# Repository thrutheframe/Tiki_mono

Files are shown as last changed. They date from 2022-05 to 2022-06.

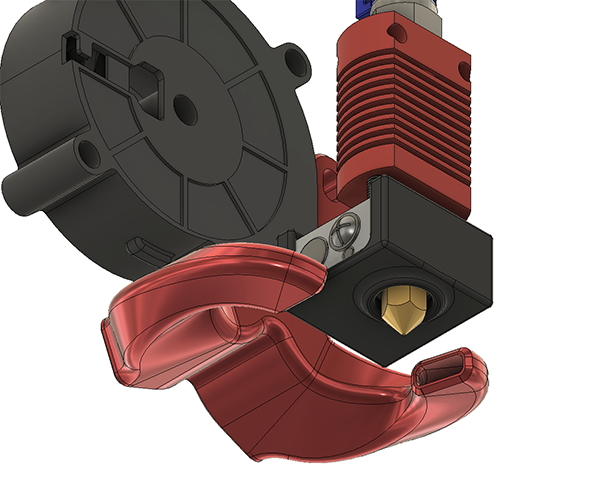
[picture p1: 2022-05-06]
images/5015 fanduct 02.png

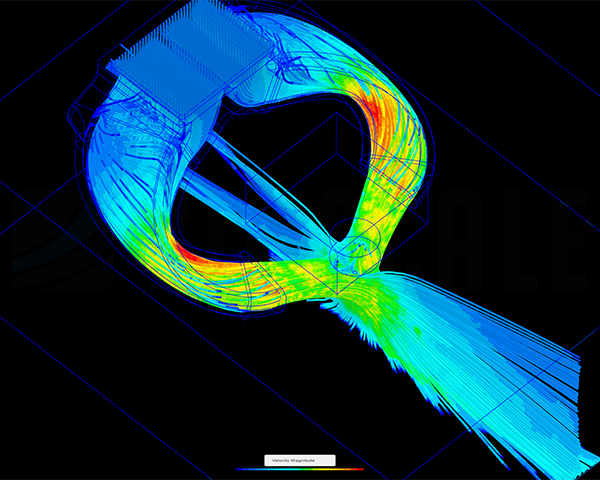
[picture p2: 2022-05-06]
images/CFD 1.png

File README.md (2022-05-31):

# Tiki Monocoque 

Tiki Mono 01

## UPDATE: 31 May 2022
Finding on Tiki Monocoque when I did input shaper calibration using ADXL345 https://github.com/thrutheframe/Tiki_mono/blob/main/update220531.md

## Introduction
Welcome to Tiki Monocoque github page. 

Since the launch of Tiki 3.2 in September 2021, I had done several updates to the design to improve the overall printability and functionality. In addition, I have been working on other projects ie the Donki direct drive extruder and had learned alot (and still learning) in terms of designing a carriage and fan mount system.  In the 2022, I set out to do several things. Learn how use Klipper (done), design and build a bare-bone printer (in progress) and do an update on the Tiki system. 

The original goal of the designing the Tiki was to have a better fanduct system for creality Ender 5. But as time pass, and buying an Orbiter V1.5, I decided to adapt the design for it. That is how Tiki3 came about. Initially my design of the main body takes inspiration from Hangtight (thingiverse) with the side mounted hotend fan and front mounting fanduct. To put things into persepctive, I did not recieve any help nor step files from anyone. I redesign it from ground up to improve printability, incoporated BL touch bracket, cable relief and a mount for the Orbiter. At that time, only thing that I used was the fanduct design because my Fusion360 skills were not good enough. Subsequently, I design the my own 5015 fan duct from scratch. 

Following the path of Tiki3, Tiki Monocoque is designed to support the Orbiter V1.5. If you like using the design and want to support my work, a contribution to my fun-funds at https://www.paypal.com/paypalme/shannonheng will be greatly apperciated. If you want to use the design for commerical/academical intend, do contact me for permission or collaborations. 

## Description
Tiki Monocoque as its namesake is a one piece printed body construction with the fanduct, BL Touch, Orbiter and ADXL345 mounted to it. This approach in design improves rigidity and dimension accuracy. The fanduct is re-wored with input from previous designs. All parts are design with intergrated supports. The fanduct is designed with overhangs of under 60 degree to the horizon. Tiki Monocoque will only work with the parts it is design with. It is lighter that its predecessor, use less material/screws and less parts to print. Please read the instructions below. 

Tiki Monocoque is designed for Creality Ender and CR machines, namely
- Ender 3/3pro/3V2
- Ender 5/5pro/5plus
- CR10 (old version)
- Ender clones with same M5 and screw positions

Hotend that has been designed for:
- Creality stock CR10 hotend (tested)
- Mellow NF-Zone CR10 (tested)
- Mellow NF Zone CR10 (tested)
- Mellow NF-Smart 
- MicroSwiss All Metal and clones

## Instructions
<i>The Instructions section will be updated accordingly when needed.</i>
- You need to reuse the 4010 coaxial fan to cool the hotend. A 5015 radial fan is required for the part cooling fan.
- This carriage/fanduct system uses M3 screws and M3 (4.6D3L) brass inserts. Only the 4010 fan and ADXL345 screw holes will be self tap. The rest will need the m3 brass inserts for better mountung the Orbiter V1.5, fanduct and BL bracket. I will NOT be designing M3 self-tapping version holes. 
- There are 4 printed parts:
    1. Tiki_M Body.stl or Tiki_M Body teardrop.stl
    2. Tiki_M Fanduct.stl
    3. Tiki_M BLbracket.stl
    4. Tiki_M cover.stl or Tiki_M cover 0_2mm offset.stl
- The BL touch offset is X=30 Y=0
- There are 2 versions of the body. One has the vertical holes in teardrop shape to improve circular print and lesser overhangs.
- There are 2 versions of the cover. The version with 0.2mm offset is smaller in size. If you are not sure which will fit, print both the covers. 
- Supports for the body and fanduct are intergrated into the design. The tip of the fanduct is under 60 degree overhang.
- If you are using an all-metal hotend, the Ptfe tube should be sticking out of the bracket about 11-11.5mm. If you are using the stock heatbreak where the ptfe tube touches the nozzle, use a 12-12.5mm length. see image
ptfe length

- Print orientations:
print orientation

## Screw BOM
- m2x4mm 2pcs : securing the adxl345 to body.
- m3x8mm 2pcs : securing Orbiter V1.5 to body
- m3x8mm 4pcs : securing BLT & blbracket to body
- m3x10mm 2 or 4pcs : securing 4010 fan to body
- m3x16mm 2pcs : securing fanduct to body
- m3x20mm 2pcs :securing hotend and body to carriage
- m4x20mm + nut 1set: securing 5015 fan to fanduct

## FAQs

Q: Is there any major design changes between this version (Tiki Monocoque) and the previous versions that are uploaded on Thingiverse?

A: Yes, there are lot of changes. Tiki Monocoque is not compatiable with parts from previous versions. 

Q:Will there be a design for V6 /Dragon hotend?

A: Not at the moment.

Q: Would you be able to include a one off custom design for probe bracket/fan duct for other fans etc?

A: Not at the moment. 

Q: Will this system fit the Sovol/Tronxy/TwoTrees etc etc?

A: Maybe. You have to print and test as I do not have those printers. 

Q: Would you release the STEP file for others to remix your design?

A: STEP files for the body and bracket will be release in the later date. STEP files for the fanduct will not be released. 

Q: Did you test print it in PLA? How did you get even get such specific numbers? "...I find stuff like this very misleading with serious potential to cause damage to printers when people try to do it..." 

A: I will try my best to answer questions pertaining to the design. Constructive suggestions and contributions to the design are greatly apperciated. Be polite and have manners in your questions. Patronizing or rude statment will be deleted. 

Q: How accurate is the CFD simulation on your fan duct? Did u consider turbulance of of the 5015? Did u take into account of hotend movement? etc etc.

A: My basic CFD simulation of the particles movement (air) is to provide a validation that the air is directed under the nozzle when designing the fan duct. There are many other parameters that I would not know. It's a fanduct for 3D printer, not a cooling system of a nuclear plant. if you do not feel confident in the design, don't use it. 

Q: Why it is called Tiki?

A: Tiki was the name of our family dog. He passed away several years ago and we still miss him dearly. So I named this system after him. 

### My 2 cents worth
STL files and documentations are free for you to download on this github page. There is NO patreon or membership needed to get access to stl, docs or exclusive support. I have always enjoyed working on Tiki for the Orbiter V1.5 and will continue to do so with no additional agenda. 3d printing is a hobby and any contribution goes to my fun-funds where I use the money on more 3d printer stuff. 

I will try to answer or help when I have the time and energy. This is because I am running other design projects concurrently. There are many fanduct systems out there, and all have it advantages and disadvantages. I try my best to improve Tiki system, and constructive suggestions are greatly appreceiated. But I do not like being patronized nor talk down to.

Credits... this is a tricky subject. While I believe it is important to give credits where its due. I do not want a situation the likes of Elon's Tesla crediting Benz for inventing the first autowagen.

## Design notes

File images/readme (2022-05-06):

Images of Tiki Monocoque mount and fan duct system.

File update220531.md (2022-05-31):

## Update 31/5/2022
In the course of the service/upgrade of my Ender 5 with Tiki Monocoque and Klipper firmware, I did the input shaping calibration using ADXL345. The Y movement graph that tells me I can safely use either MZV or EI shaping with an acceleration 3000mm/s/s (which is half of the max acceleration recommended). 

y

On the other hand, the X movement shows a very different result. With a wide spike on the PSD from 90 -133Hz. Initially I thought some screw was not properly tightened, it turned out that the wide spike is because I used 2 screws instead of 4 to secure the 4010 fan on the side. 



After securing the fan, the spike got slimer with PSD starting from 100-133Hz. It was very obvious as the buzzing noise starts around 102Hz onwards. I left me puzzled, what can cause this spike at the higher frequency? I would definitely not use the recommended 3HUMP_EI as it is too aggressive and can cause rounded edges. I can still use MZV and keep to the 3000mm/s/s acceleration. But I wanted to know if the spike was caused by a design flaw on my side. 



The first change I did was to switch from spreadCycle to stealthChop to see if there was any difference. There was a drop in PSD values, and the spike became less pronounced. This means I can use less aggressive shaper ie MZV and higher accelerations. But that does not resolve the spike at higher frequency. I would rather use spreadCycle for accuracy and cooler stepper motor.  



Looking at the design of Tiki Monocoque, I asked myself, what can cause the vibrations at high frequency? The 4010 fan, NF-Zone hotend and BL touch are close to the mounting points and should not to be the problem. The fan duct and 5015 fan is light weight and firmly mounted as close to the mount points as possible. 
I narrow down to the way the Orbiter v1.5 was mounted, while the base contact and the two M3 screws secures the orbiter firmly to the main body, the position of LDO motor is away from the CG of the whole system. I removed the Orbiter, switch back to spreadCycle and re-ran the x resonance test again. The results show that my guess was right, the spike was gone. 

Tiki Mono 01d



From what I deduced, there are 2 ways I can go:
1.	Redesign the mount to have the LDO motor point to towards the mounting point, giving better CG to the system. The is the difficult way as redesigning the mount involve making other compromises to the stability of the mount. The constraints are due to the design of the Orbiter v1.5 and the Creality carriage plate. 

2.	Print at a slower acceleration and speed. This is the choice I decide to go along with. With this existing design, I was able to print at a velocity of 120mm/s and 3000/s/s acceleration with no drop in quality and precision. That is 2X in velocity and 4X in acceleration compared to stock Bowden system on an Ender 5. IMO that is pretty good. Maybe others can do better, but I am satisfied with these numbers. For real printing situation, I don’t go above 100mm/s as my costing formula is based on print time, and those who engage me to print are looking at quality of finish rather than speed of prints.

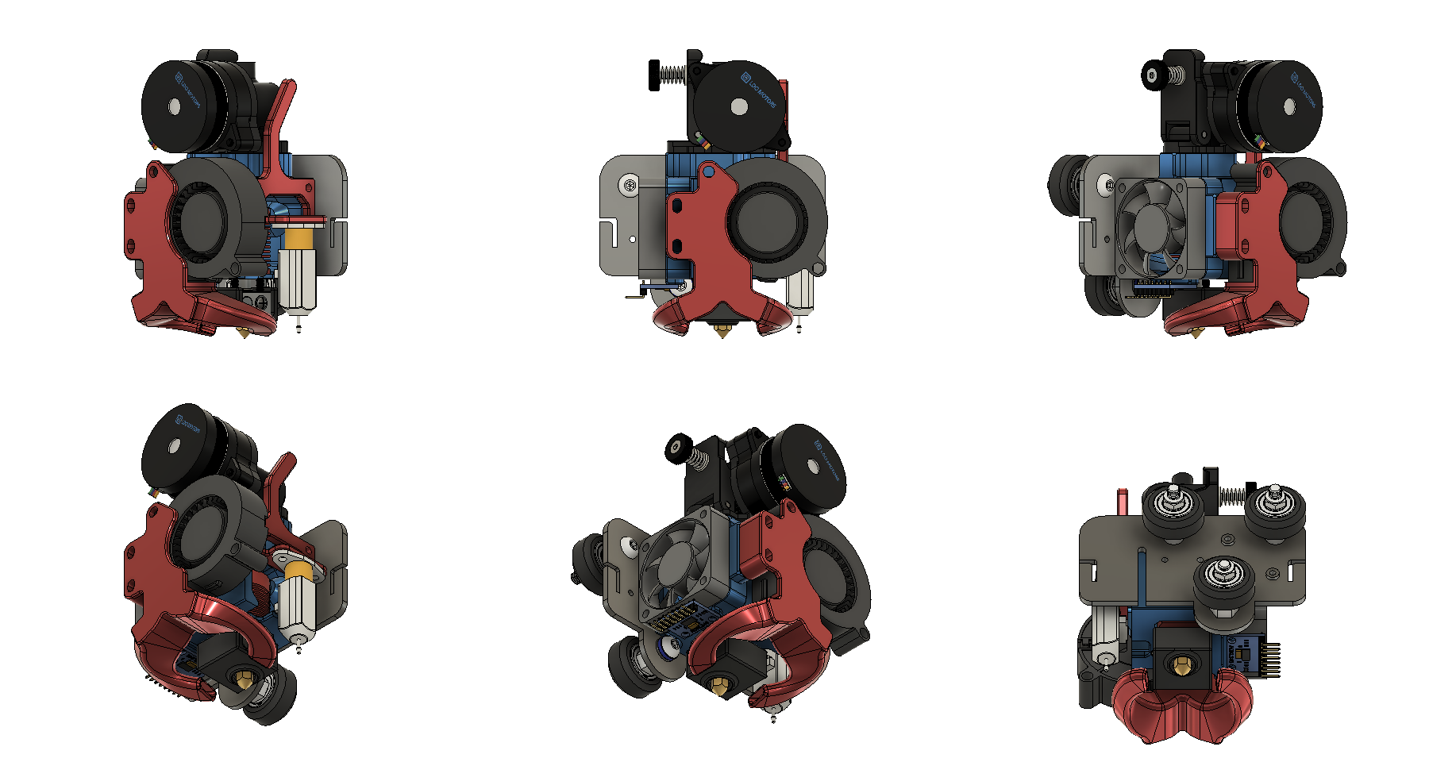
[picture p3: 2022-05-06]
images/Tiki Mono 01.png

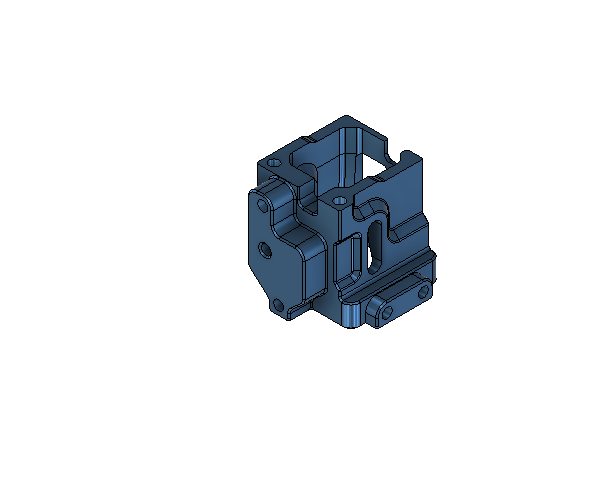
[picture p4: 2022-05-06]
images/Tiki Mono body 2.png

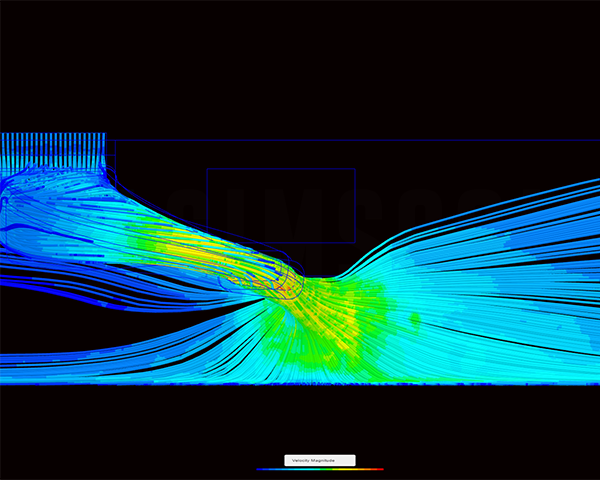
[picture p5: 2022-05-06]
images/CFD 2.png

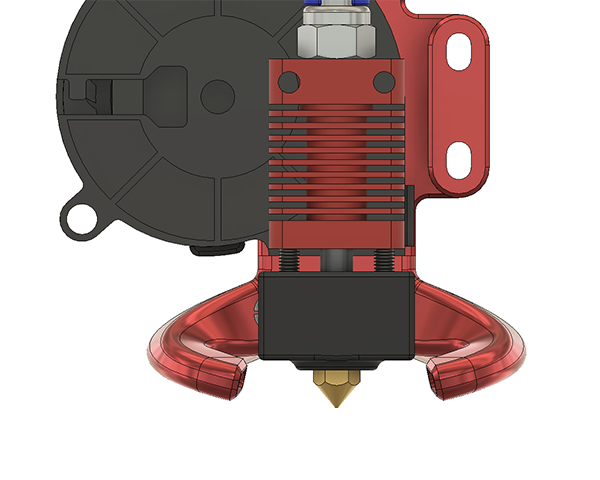
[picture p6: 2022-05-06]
images/5015 fanduct 01.png

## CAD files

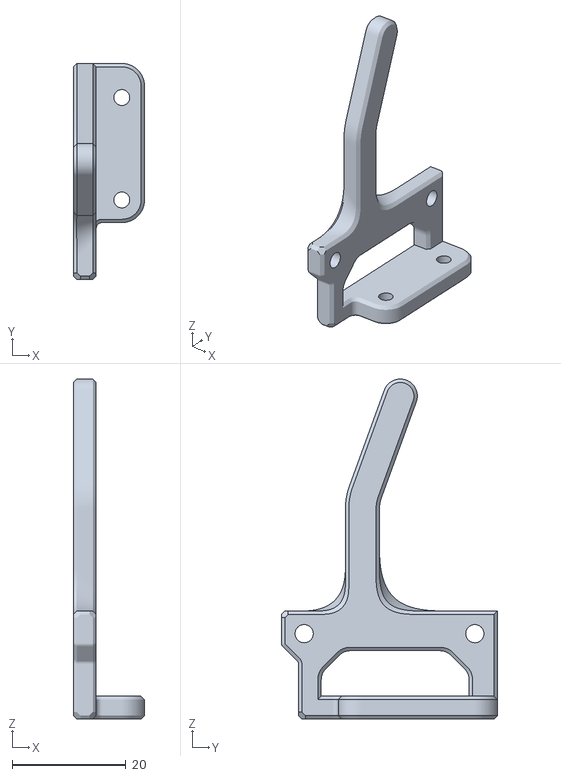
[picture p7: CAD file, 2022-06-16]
STL/Tiki_M BL bracket.stl
12.5 x 38.0 x 59.8

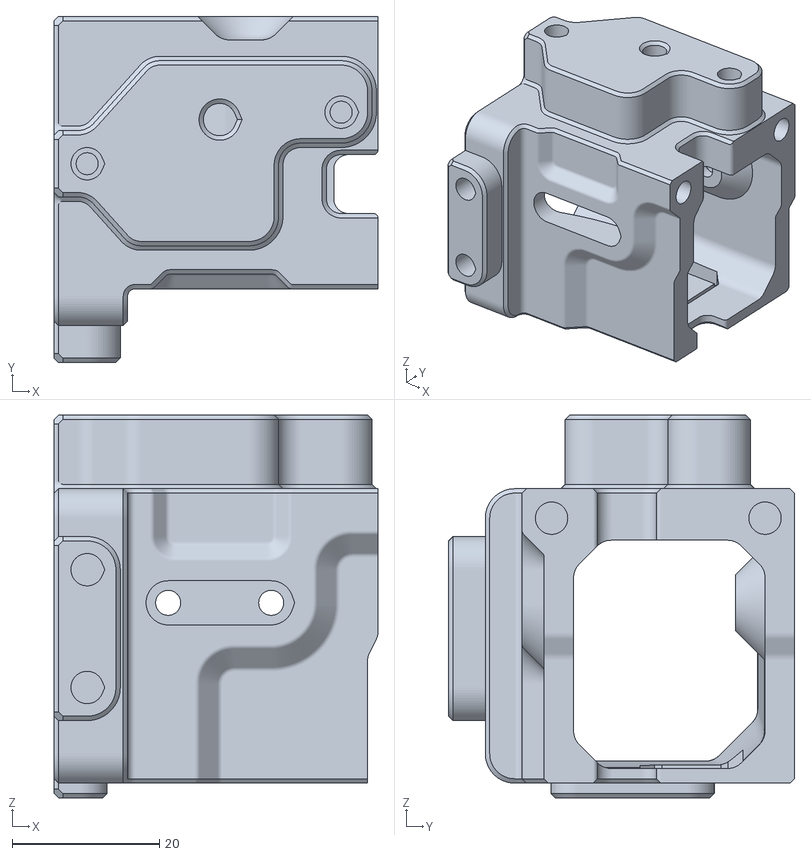
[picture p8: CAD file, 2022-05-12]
STL/Tiki_M Body teardrop.stl
44.0 x 47.0 x 52.0

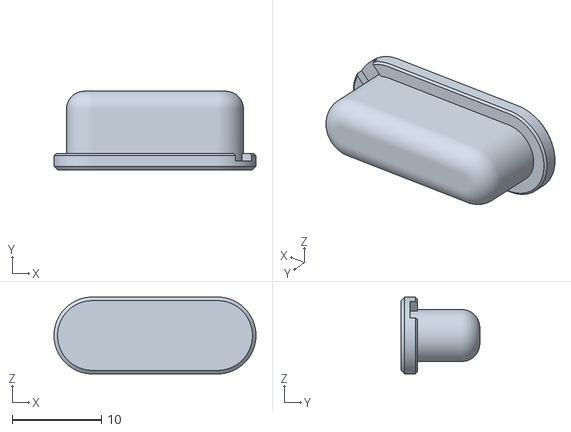
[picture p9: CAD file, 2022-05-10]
STL/Tiki_M cover 0_2mm offset.stl
22.6 x 8.80 x 8.60

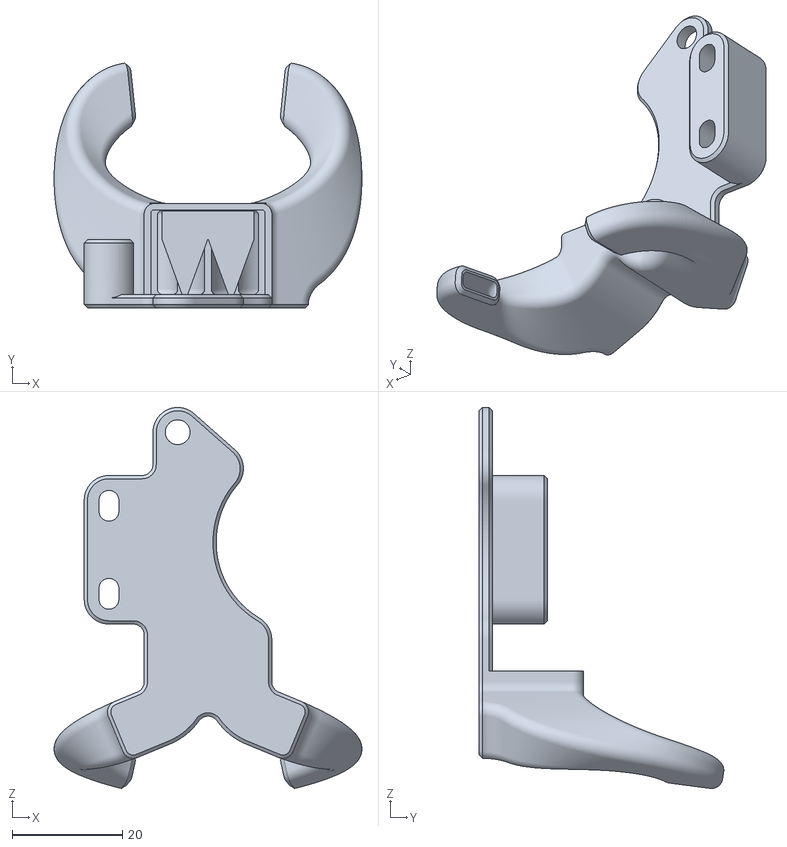
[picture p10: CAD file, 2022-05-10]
STL/Tiki_M Fanduct.stl
55.9 x 44.5 x 69.2

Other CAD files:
STL/Tiki_M Body.stl
STL/Tiki_M cover.stl

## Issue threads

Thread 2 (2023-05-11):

Bl touch bracket holes not aligned with body

teerapat-udo, 2023-05-11:
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

Not sure if you're still maintaining this, but the holes in the bl touch bracket aren't aligned with the holes in the body. Pic borrowed from the orbiter FB group.

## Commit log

2022-05-06 fan duct images
2022-05-12 Delete Tiki_M Body.stl
    due to update and name change
    [Tiki_M Body.stl]
2022-05-12 uploadmain body files
    [Tiki_M Body teardrop.stl, Tiki_M Body.stl]
2022-06-16 Add files via upload
    update design to give more 1mm more off_set
    [Tiki_M BL bracket.stl]
